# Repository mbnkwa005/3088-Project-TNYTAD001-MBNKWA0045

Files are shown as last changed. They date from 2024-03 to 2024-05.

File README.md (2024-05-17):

# EEE3088F Micro-Mouse Project

### Authors
- Tadiwa Tanyanyiwa
- Kwanele Mabanga

Welcome to the GitHub repository for our project!, which includes two key submodules: the Power submodule and the Sensing submodule.
This repository serves as a central hub for managing and sharing all the relevant files, including datasheets, schematics, and code associated with each submodule.

## Submodules

### Power Submodule
The Power submodule is responsible for supplying the necessary electrical power to all components of the project. 
It ensures that all components are properly powered under different operational conditions.

### Sensing Submodule
The Sensing submodule deals with acquiring data from the physical environment through sensors.

## Repository Contents

- **Datasheets** - Contains all the technical datasheets for components used in both submodules. This includes information on specifications, usage, and limitations of components such as sensors and power management chips.

- **Schematics/Documentation** - Provides detailed pdf schematics for the design and layout of the electrical circuits used in the project. This includes diagrams for both the Power and Sensing submodules as well as the BOM files for each submodule

- **KiCad** - This folder contains all the KiCad Gerber files and KiCad schematics for each subsection.
- **Software** - This folder contains the code used to test the functionalty of the sensing subsystem.
  
### What Hardware you will need
- An STM32L476 Microcontroller
- STM Discovry Board with a STM32F051 Microcontroller (For Testing)
- A micro USB cable to flash code into the STM32FO microcontroller.

### What Software you will need
- STM32CubeIDE 1.13.1 (or newer version) or VSCode with STM32 Extension
- KiCAD 7.0 (or newer version)

## Additional Resources

For more information on specific components or for help with the setup and operation of the submodules, please refer to the datasheets and schematics found in their respective directories within this repository.

## Acknowledgments
Thank you to the UCT Electrical Engineering Department for allowing us to do this cool project!

## Contact

For further inquiries or issues, please contact Tadiwa (tnytad001@myuct.ac.za) and Kwanele (mbnkwa005@myuct.ac.za).

Thank you for visiting our project repository!

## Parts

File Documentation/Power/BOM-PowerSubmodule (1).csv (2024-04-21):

Comment | Designator | Footprint | LCSC
1k | R1,R2,R3,R4 | R_0402_1005Metric | C11702
0.01uF | C3 | C_0402_1005Metric | C15195
0.1uF | C1 | C_0402_1005Metric | C1525
10uF | C2,C5 | C_0603_1608Metric | C19702
LED | D1 | LED_0603_1608Metric | C2286
LED | D2 | LED_0805_2012Metric | C2297
10k | R5 | R_0402_1005Metric | C25744
DRV8833PWP | U2 | HTSSOP-16-1EP_4.4x5mm_P0.65mm_EP3.4x5mm_Mask2.46x2.31mm_ThermalVias | C50506
TP4056 | U1 | SOP127P600X175-9N | C725790
2.2uF | C4 | C_0402_1005Metric

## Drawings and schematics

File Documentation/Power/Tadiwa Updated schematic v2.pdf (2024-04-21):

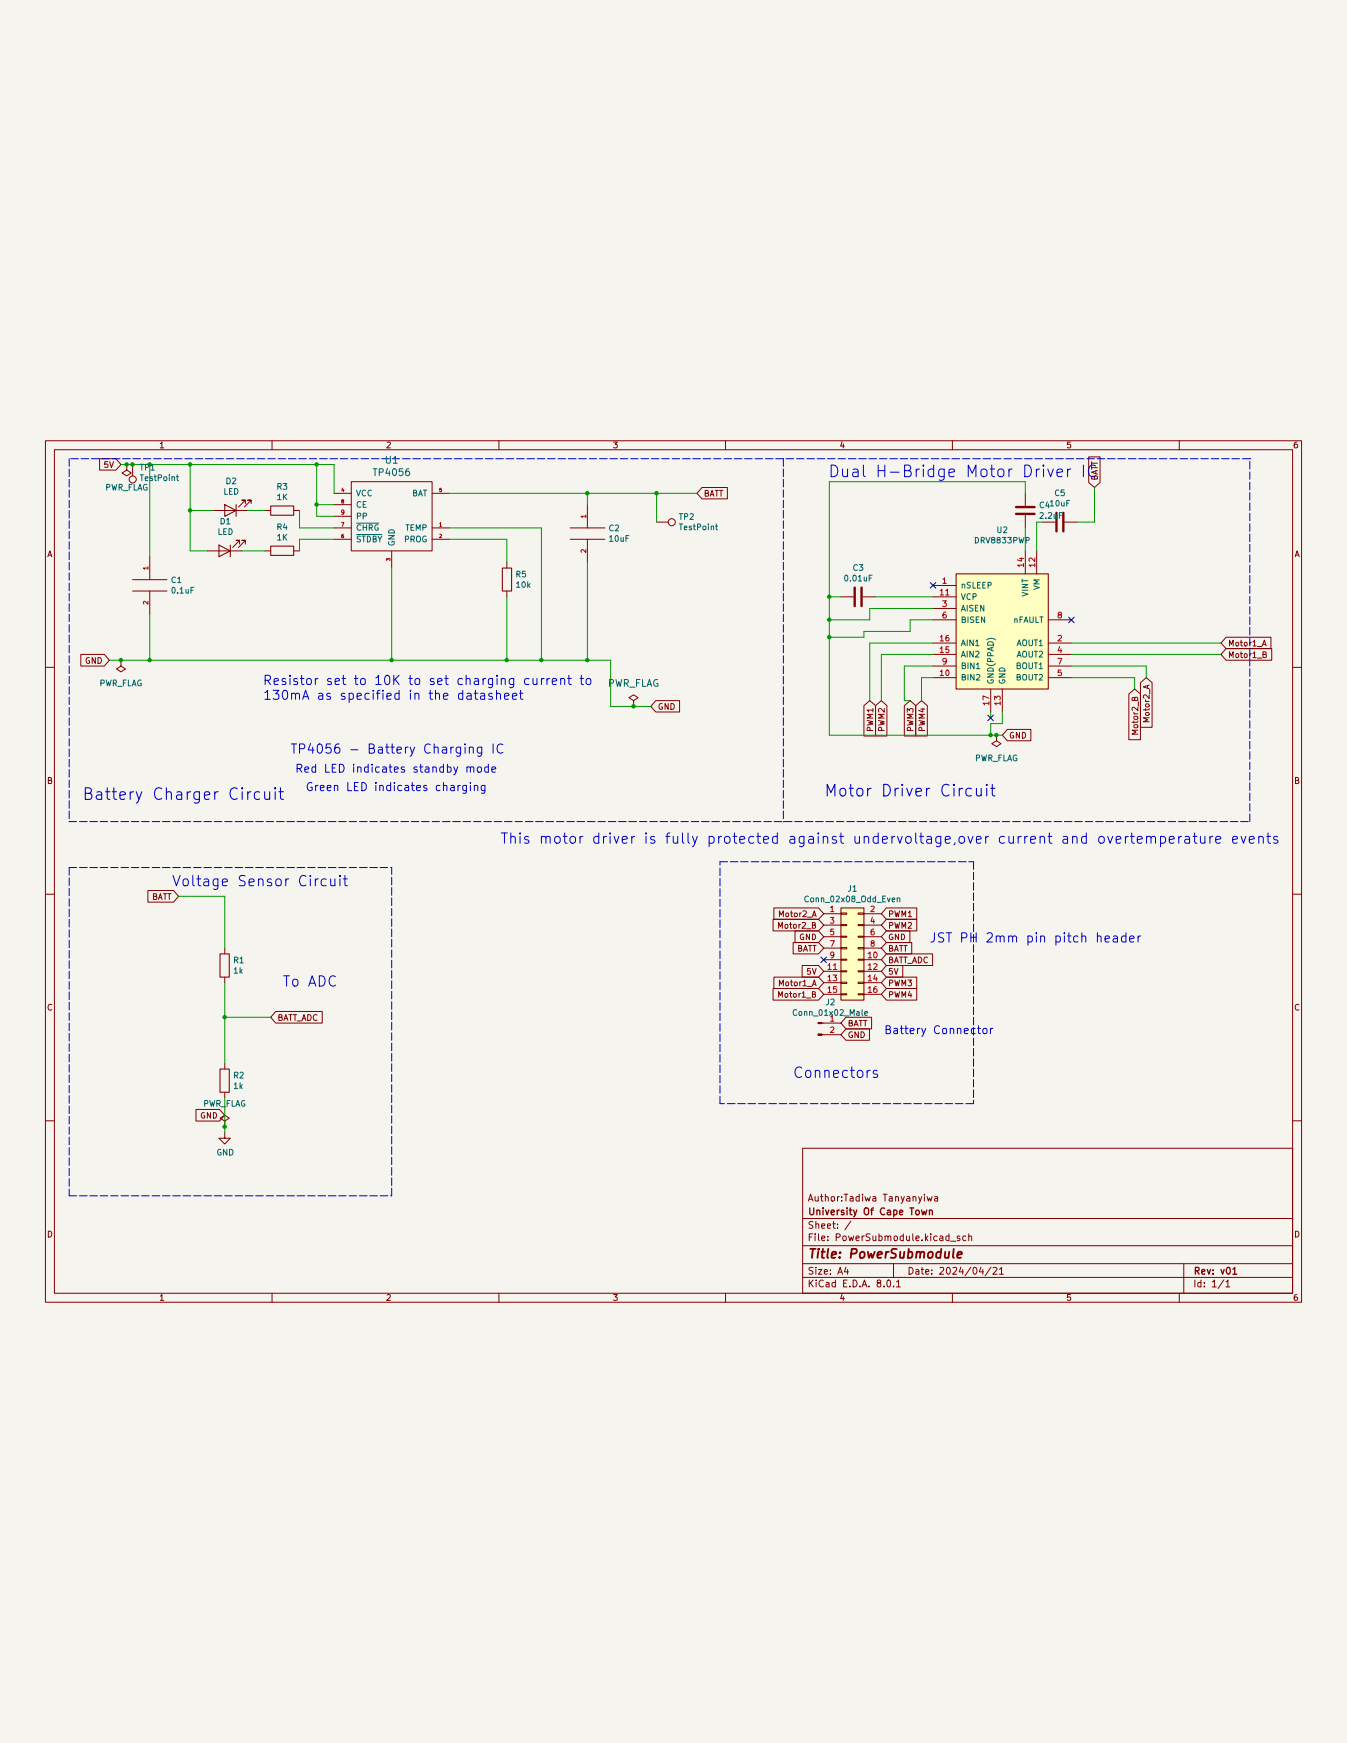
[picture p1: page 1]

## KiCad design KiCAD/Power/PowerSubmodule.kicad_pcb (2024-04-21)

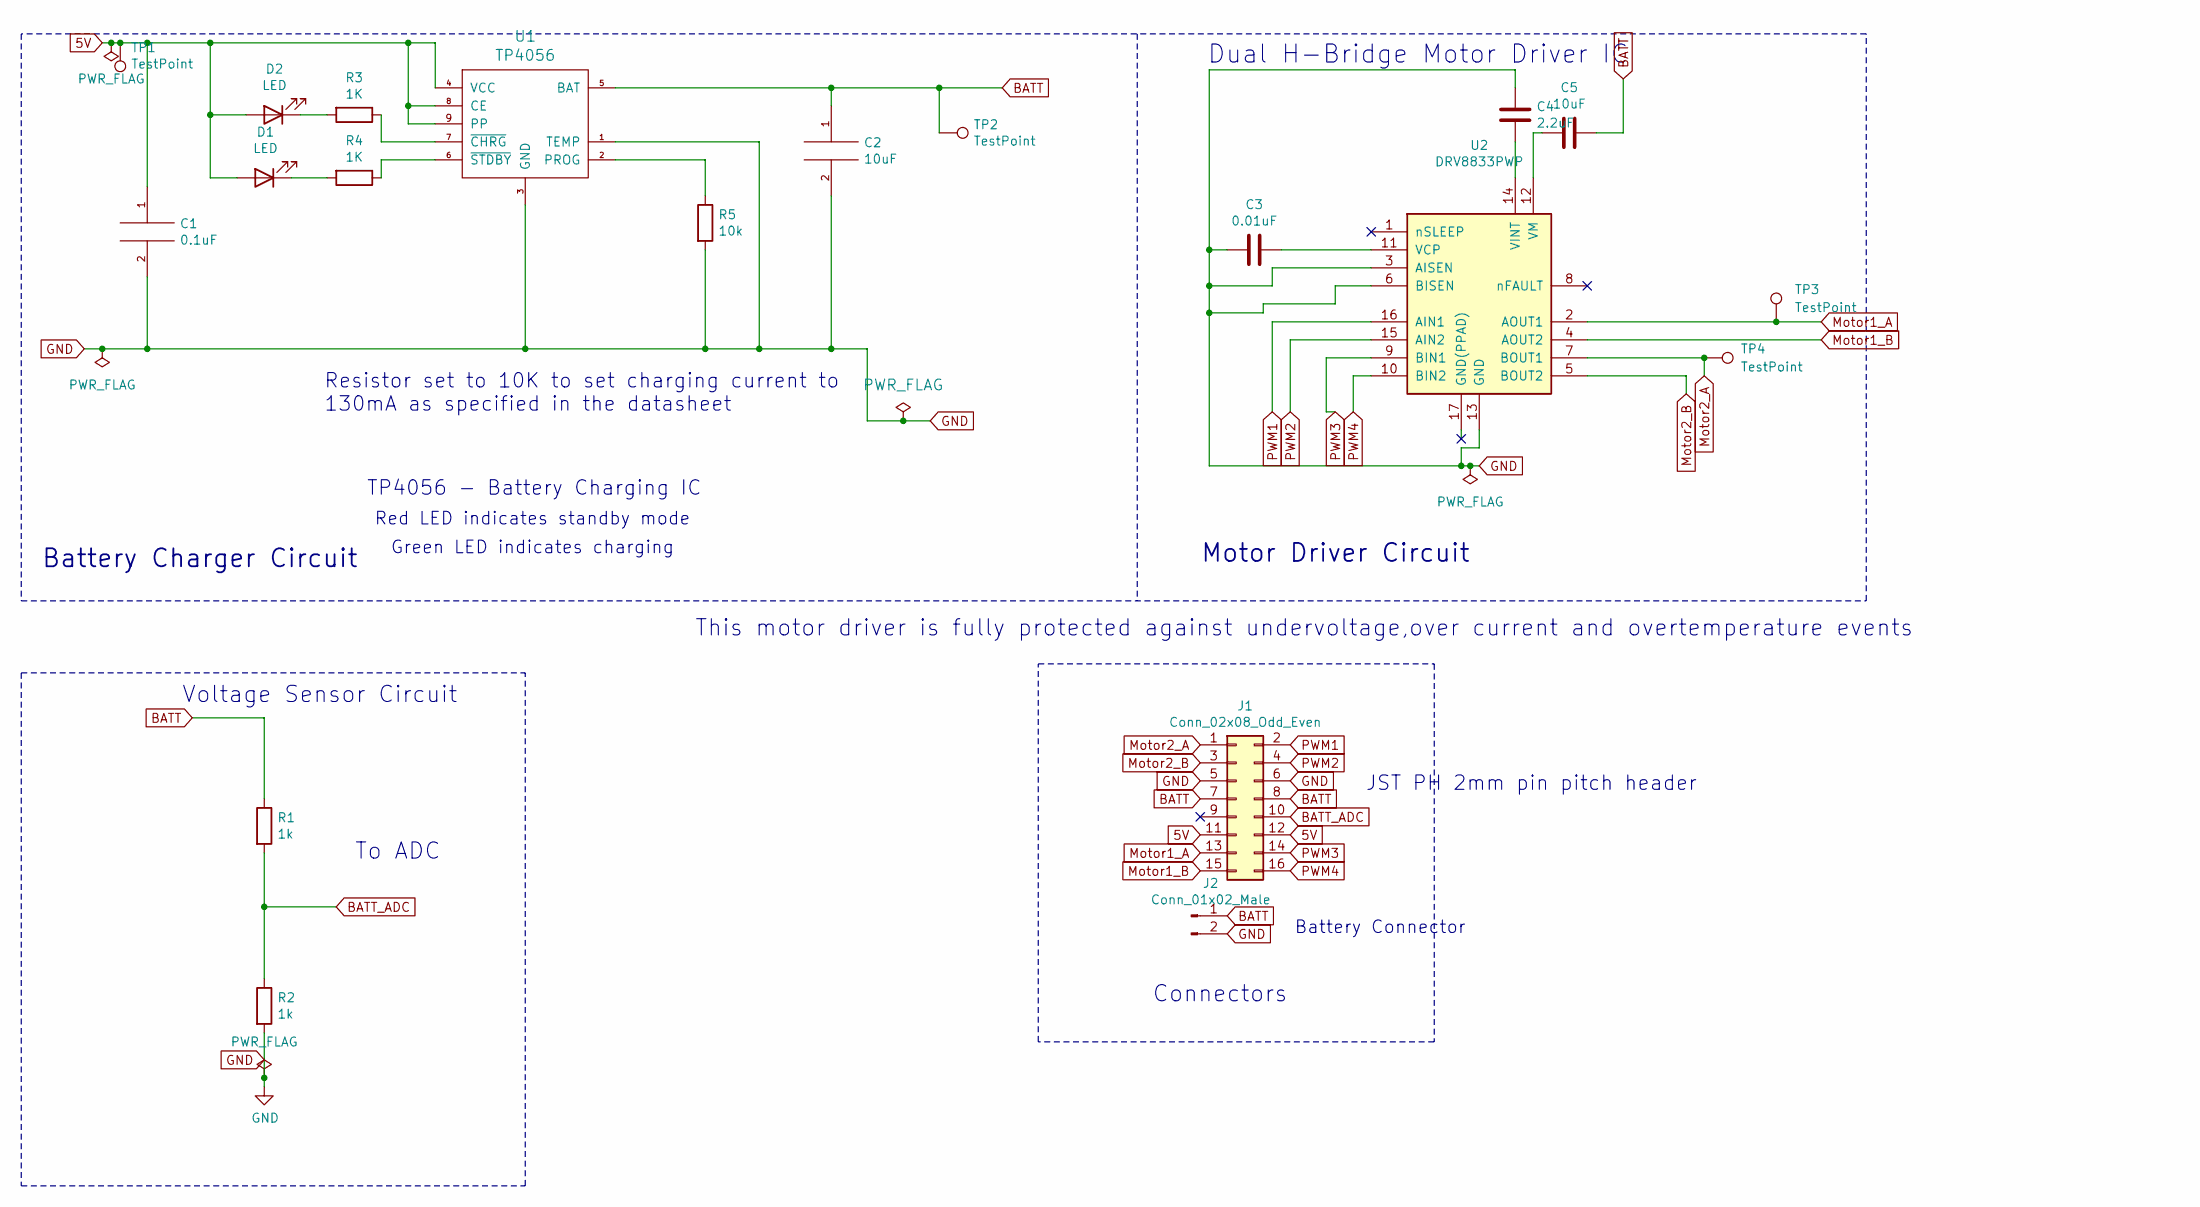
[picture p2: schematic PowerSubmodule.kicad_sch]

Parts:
C1: 0.1uF; C_0402_1005Metric
C2, C5: 10uF; C_0603_1608Metric
C3: 0.01uF; C_0402_1005Metric
C4: 2.2uF; C_0402_1005Metric
D1: LED; LED_0603_1608Metric
D2: LED; LED_0805_2012Metric
J1: Conn_02x08_Odd_Even; PinHeader_2x08_P2.54mm_Vertical
J2: Conn_01x02_Male; JST_JWPF_B02B-JWPF-SK-R_1x02_P2.00mm_Vertical
R1, R2: 1k; R_0402_1005Metric
R3, R4: 1K; R_0402_1005Metric
R5: 10k; R_0402_1005Metric
TP1: TestPoint; TestPoint_THTPad_D1.0mm_Drill0.5mm
TP2: TestPoint; TestPoint_THTPad_D1.5mm_Drill0.7mm
TP3, TP4: TestPoint
U1: TP4056; SOP127P600X175-9N
U2: DRV8833PWP; HTSSOP-16-1EP_4.4x5mm_P0.65mm_EP3.4x5mm_Mask2.46x2.31mm_The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

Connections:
5V: C1.1, D1.2 (A), D2.2 (A), J1.11, J1.12, TP1.1, U1.4 (VCC), U1.8 (CE), U1.9 (PP)
BATT: C2.1, C5.1, J1.7, J1.8, J2.1, R1.1, TP2.1, U1.5 (BAT)
BATT_ADC: J1.10, R1.2, R2.1
GND: C1.2, C2.2, C3.1, C4.1, J1.5, J1.6, J2.2, R2.2, R5.2, U1.1 (TEMP), U1.3 (GND), U2.3 (AISEN), U2.6 (BISEN), U2.13 (GND)
Motor1_A: J1.13, TP3.1, U2.2 (AOUT1)
Motor1_B: J1.15, U2.4 (AOUT2)
Motor2_A: J1.1, TP4.1, U2.7 (BOUT1)
Motor2_B: J1.3, U2.5 (BOUT2)
unnamed: D1.1 (K), R4.2
unnamed: D2.1 (K), R3.2
unnamed: R5.1, U1.2 (PROG)
unnamed: R3.1, U1.7 (~CHRG)
unnamed: R4.1, U1.6 (~STDBY)
unnamed: C3.2, U2.11 (VCP)
unnamed: C4.2, U2.14 (VINT)
unnamed: C5.2, U2.12 (VM)
PWM1: J1.2, U2.16 (AIN1)
PWM2: J1.4, U2.15 (AIN2)
PWM3: J1.14, U2.9 (BIN1)
PWM4: J1.16, U2.10 (BIN2)

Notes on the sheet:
TP4056 - Battery Charging IC
Voltage Sensor Circuit
Battery Charger Circuit
This motor driver is fully protected against undervoltage,over current and overtemperature events
Dual H-Bridge Motor Driver IC
Motor Driver Circuit
Resistor set to 10K to set charging current to 130mA as specified in the datasheet
Connectors
Battery Connector
To ADC
Red LED indicates standby mode
Green LED indicates charging
JST PH 2mm pin pitch header

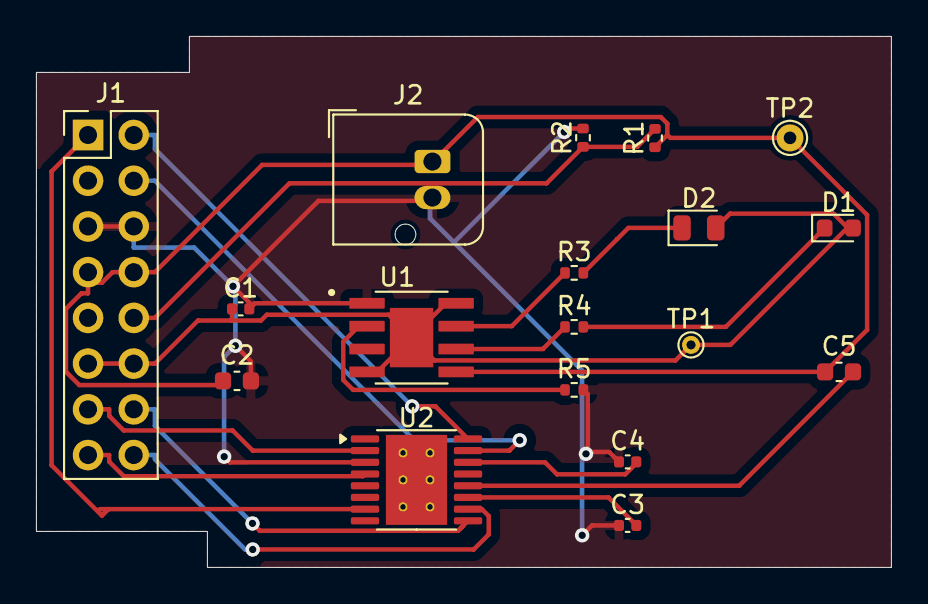
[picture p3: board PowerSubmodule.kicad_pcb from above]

Board: 2 copper layers, 47.5 x 29.5 mm, 18 parts (0 on the bottom side), 20 nets.

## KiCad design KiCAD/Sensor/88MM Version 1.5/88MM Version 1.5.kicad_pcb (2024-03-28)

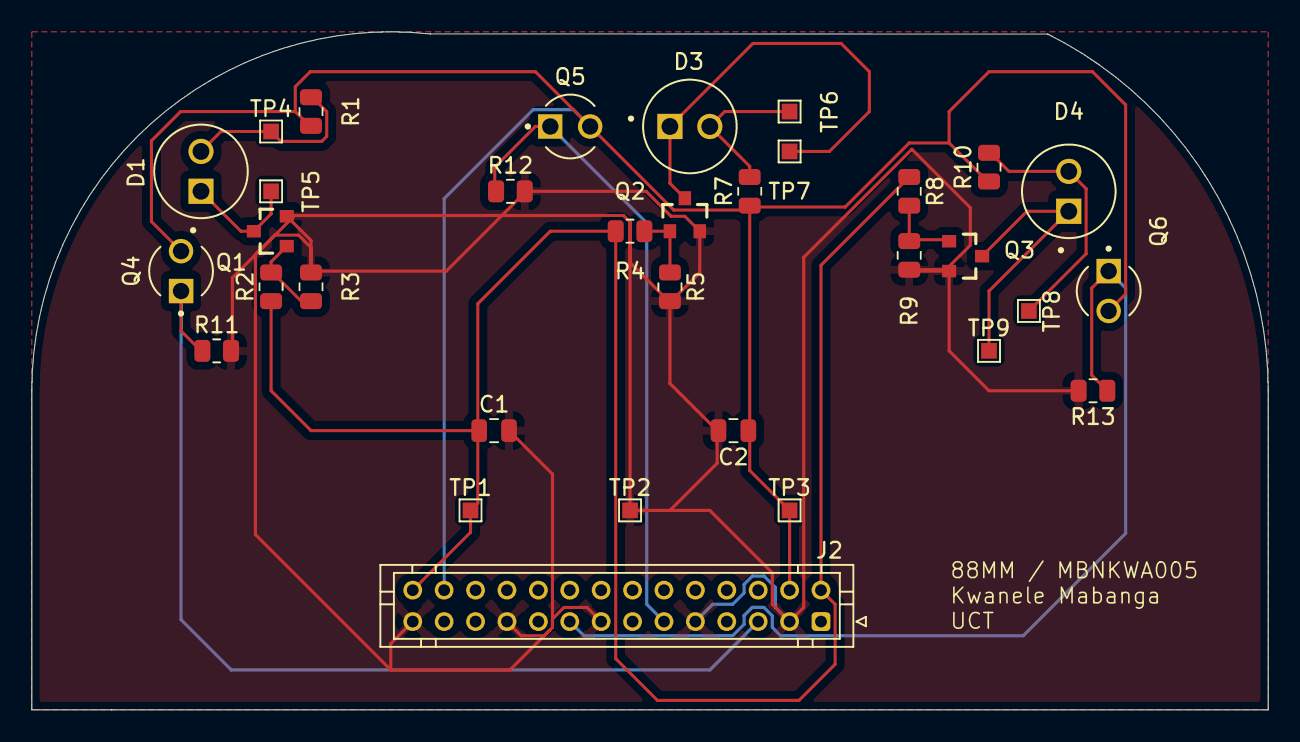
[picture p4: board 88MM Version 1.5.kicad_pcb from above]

Board: 2 copper layers, 78.7 x 43.2 mm, 33 parts (0 on the bottom side), 15 nets.

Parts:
C1, C2: 10nF; C_0805_2012Metric
D1, D3, D4: TSAL6200; LEDRD254W55D595H900
J2: Conn_02x14_Odd_Even; JST_PHD_B28B-PHDSS_2x14_P2.00mm_Vertical
Q1, Q2, Q3: MMBT5551; SOT23-3
Q4, Q5, Q6: TEFT4300; XDCR_TEFT4300
R1, R7, R10: 220; R_0805_2012Metric
R2, R4, R8: 100; R_0805_2012Metric
R3, R5, R9, R11, R12, R13: 10k; R_0805_2012Metric
TP1, TP2, TP3, TP4, TP5, TP6, TP7, TP8, TP9: TestPoint; TestPoint_Pad_1.0x1.0mm

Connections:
+3V3: C1.1, J2.2, J2.28, R2.1, R4.1, R8.1, TP1.1
+BATT: C2.1, J2.4, J2.26, Q4.C, Q5.C, Q6.C, R1.1, R7.1, R10.1, TP3.1
/IR_LED_1A: D1.A, R1.2, TP4.1
/IR_LED_2A: D3.A, R7.2, TP6.1
/IR_LED_2C: D3.C, Q2.3, TP7.1
/IR_LED_3A: D4.A, R10.2, TP8.1
/IR_LED_3C: D4.C, Q3.3, TP9.1
/IR_LED_C: D1.C, Q1.3, TP5.1
/PA3: J2.5, Q4.E, R11.1
/PA5: J2.11, Q5.E, R12.1
/PA7: J2.17, Q6.E, R13.1
GND: C1.2, C2.2, J2.3, J2.9, J2.15, J2.21, J2.27, Q1.2, Q2.2, Q3.2, R3.2, R5.2, R9.2, R11.2, R12.2, R13.2, TP2.1
unnamed: Q1.1, R2.2, R3.1
unnamed: Q2.1, R4.2, R5.1
unnamed: Q3.1, R8.2, R9.1

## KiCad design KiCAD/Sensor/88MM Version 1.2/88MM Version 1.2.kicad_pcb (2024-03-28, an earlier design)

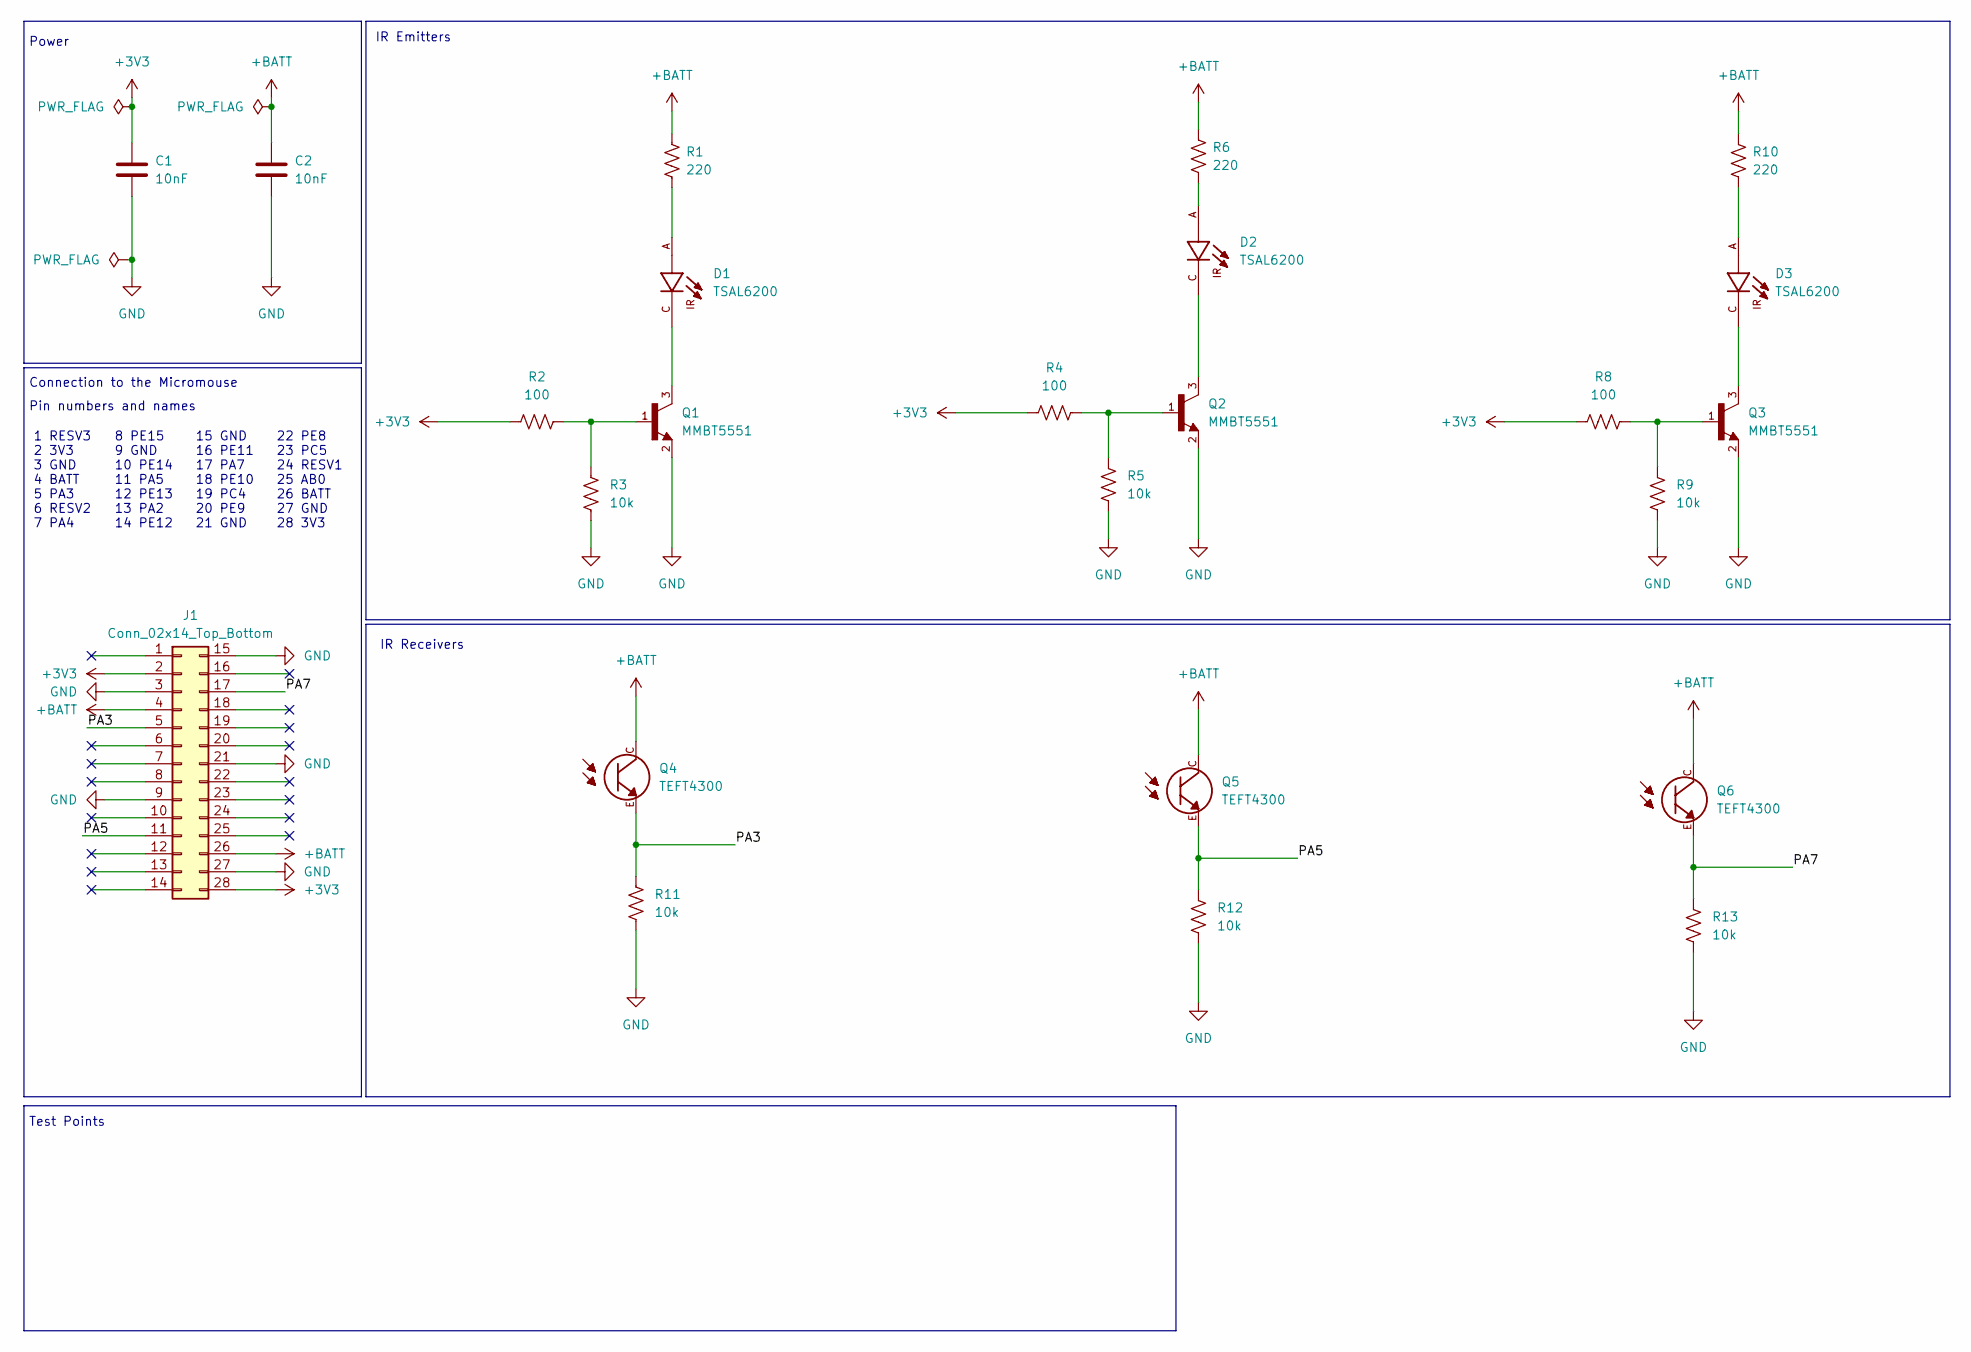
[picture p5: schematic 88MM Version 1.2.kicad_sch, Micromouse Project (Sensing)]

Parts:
C1, C2: 10nF; C_0805_2012Metric_Pad1.18x1.45mm_HandSolder
D1, D2, D3: TSAL6200; LEDRD254W55D595H900; PARTREV 2.4
J1: Conn_02x14_Top_Bottom; JST_PHD_B28B-PHDSS_2x14_P2.00mm_Vertical
Q1, Q2, Q3: MMBT5551; SOT23-3
Q4, Q5, Q6: TEFT4300; XDCR_TEFT4300; DigiKey_Part_Number 751-1041-ND
R1, R6, R10: 220; R_Axial_DIN0207_L6.3mm_D2.5mm_P2.54mm_Vertical
R2, R4, R8: 100; R_Axial_DIN0207_L6.3mm_D2.5mm_P2.54mm_Vertical
R3, R5, R9, R11, R12, R13: 10k; R_Axial_DIN0207_L6.3mm_D2.5mm_P2.54mm_Vertical

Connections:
+3V3: C1.1, J1.2, J1.28, R2.1, R4.1, R8.1
+BATT: C2.1, J1.4, J1.26, Q4.C, Q5.C, Q6.C, R1.1, R6.1, R10.1
/PA3: J1.5, Q4.E, R11.1
/PA5: J1.11, Q5.E, R12.1
/PA7: J1.17, Q6.E, R13.1
GND: C1.2, C2.2, J1.3, J1.9, J1.15, J1.21, J1.27, Q1.2, Q2.2, Q3.2, R3.2, R5.2, R9.2, R11.2, R12.2, R13.2
unnamed: D1.A, R1.2
unnamed: D1.C, Q1.3
unnamed: D2.A, R6.2
unnamed: D2.C, Q2.3
unnamed: D3.A, R10.2
unnamed: D3.C, Q3.3
unnamed: Q1.1, R2.2, R3.1
unnamed: Q2.1, R4.2, R5.1
unnamed: Q3.1, R8.2, R9.1

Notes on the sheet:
Connection to the Micromouse
Test Points
IR Receivers
Pin numbers and names
IR Emitters
22 PE8 23 PC5 24 RESV1 25 AB0 26 BATT 27 GND 28 3V3
1 RESV3 2 3V3 3 GND 4 BATT 5 PA3 6 RESV2 7 PA4
Power
15 GND 16 PE11 17 PA7 18 PE10 19 PC4 20 PE9 21 GND
8 PE15 9 GND 10 PE14 11 PA5 12 PE13 13 PA2 14 PE12

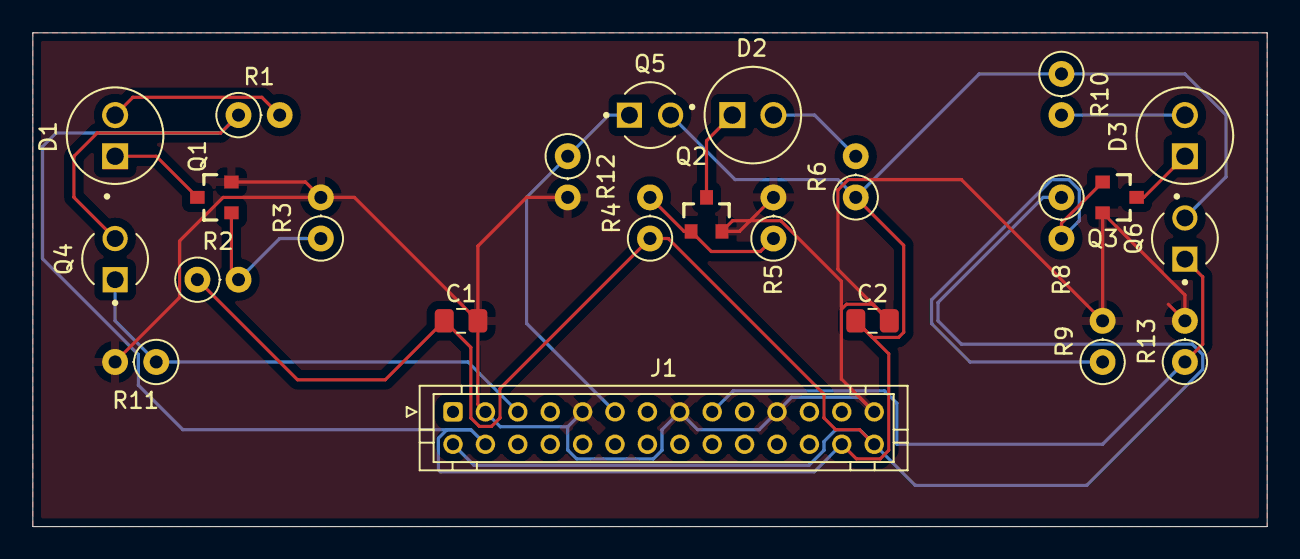
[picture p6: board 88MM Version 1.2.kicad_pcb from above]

Board: 2 copper layers, 76.2 x 30.5 mm, 24 parts (0 on the bottom side), 15 nets.

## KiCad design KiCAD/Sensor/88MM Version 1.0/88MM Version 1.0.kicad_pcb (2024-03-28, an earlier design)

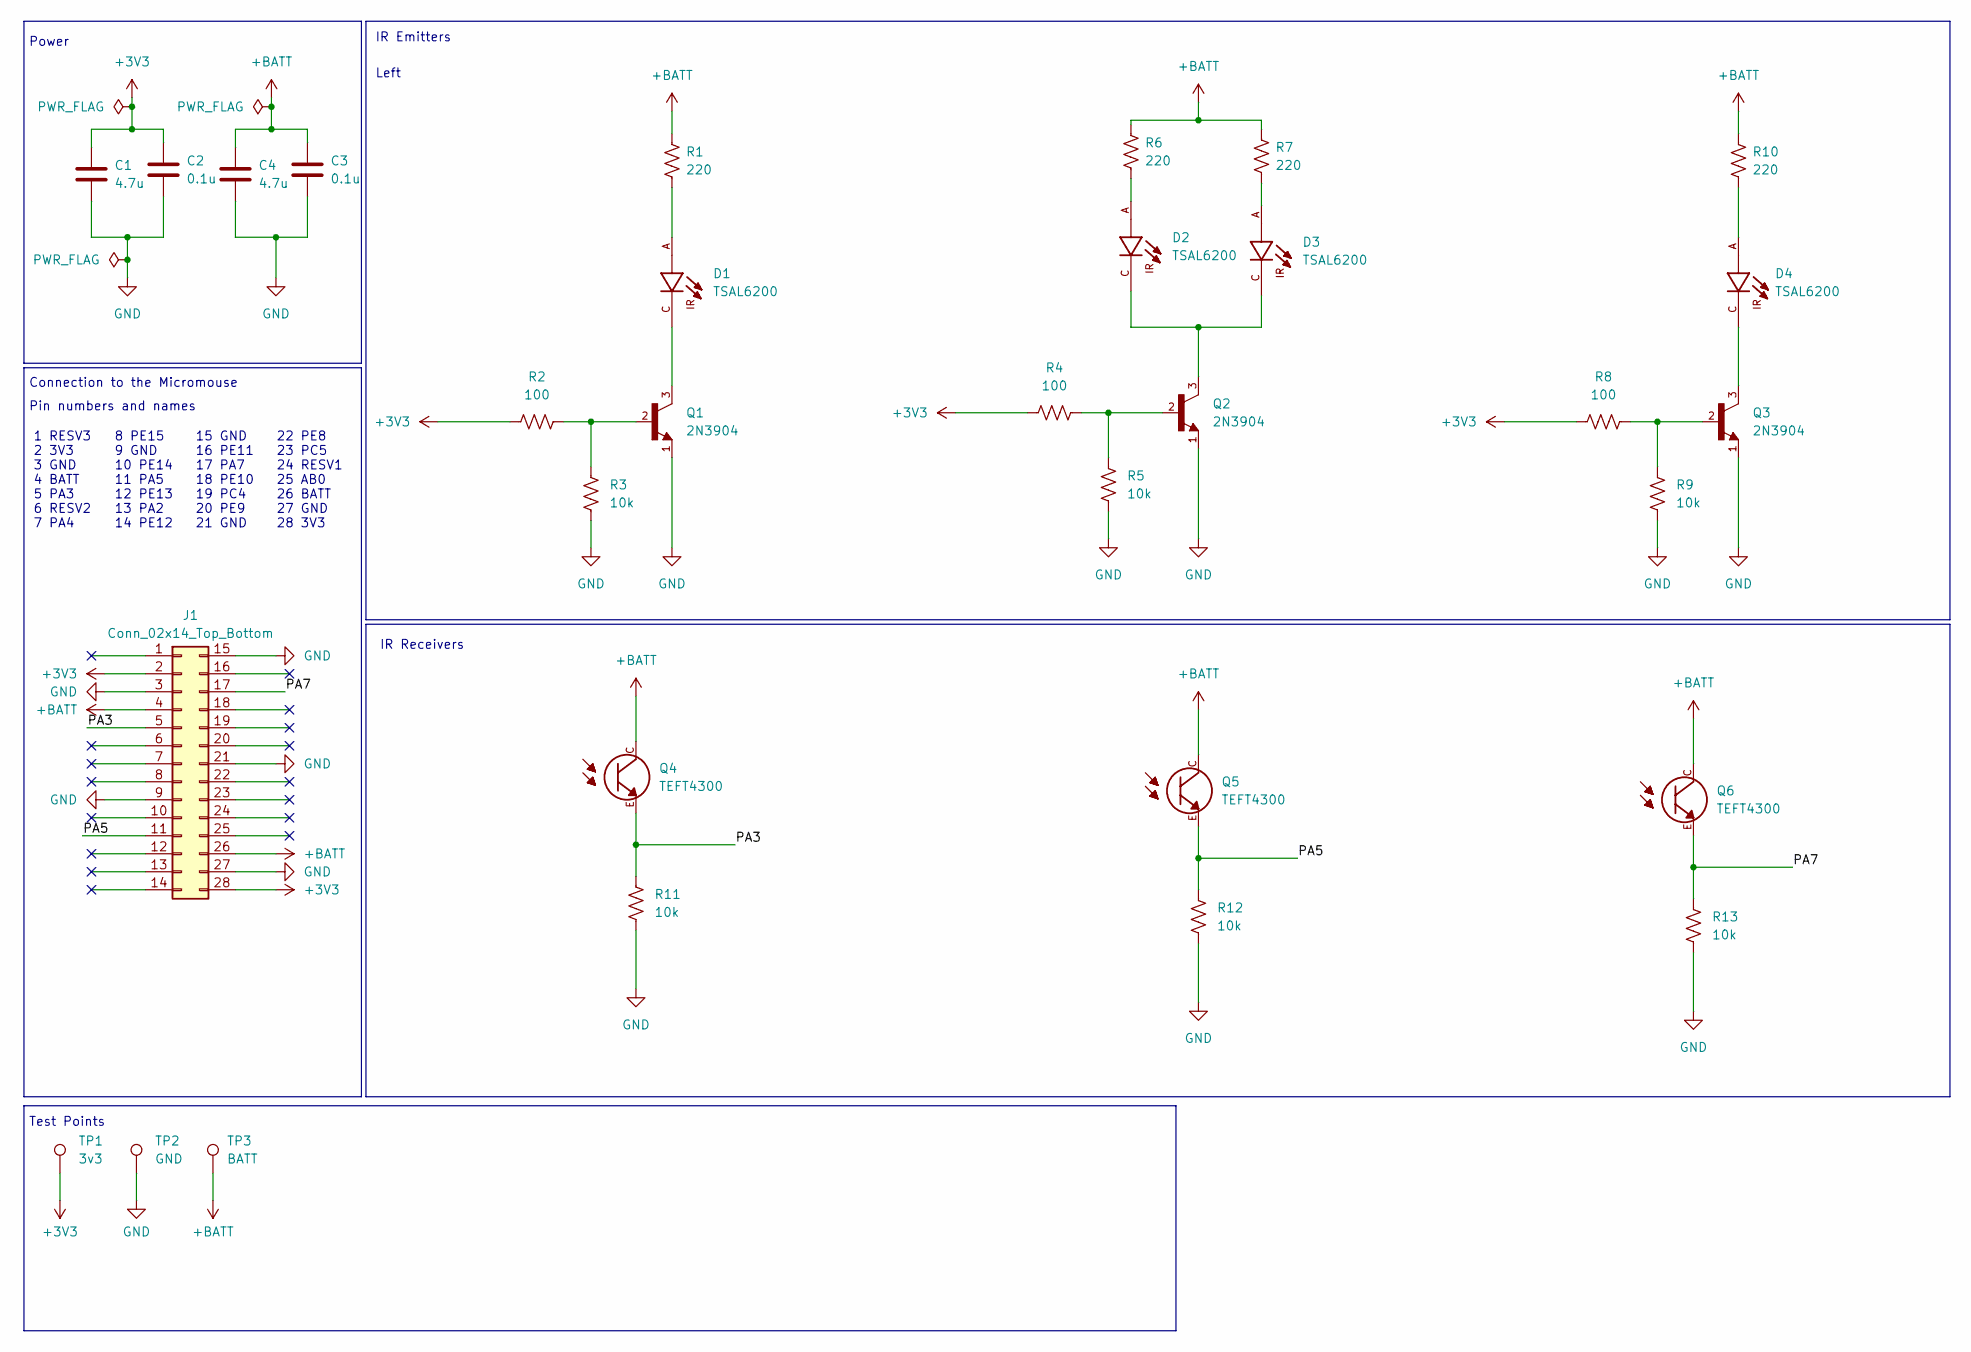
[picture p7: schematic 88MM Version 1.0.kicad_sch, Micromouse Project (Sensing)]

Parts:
C1, C4: 4.7u; CP_Radial_D5.0mm_P2.00mm
C2, C3: 0.1u; CP_Radial_D5.0mm_P2.00mm
D1, D2, D3, D4: TSAL6200; LEDRD254W55D595H900; PARTREV 2.4
J1: Conn_02x14_Top_Bottom; JST_PHD_B28B-PHDSS_2x14_P2.00mm_Vertical
Q1, Q2, Q3: 2N3904; TO92127P495H495-3; PARTREV February 2003
Q4, Q5, Q6: TEFT4300; XDCR_TEFT4300; DigiKey_Part_Number 751-1041-ND
R1, R6, R7, R10: 220; R_Axial_DIN0207_L6.3mm_D2.5mm_P2.54mm_Vertical
R2, R4, R8: 100; R_Axial_DIN0207_L6.3mm_D2.5mm_P2.54mm_Vertical
R3, R5, R9, R11, R12, R13: 10k; R_Axial_DIN0207_L6.3mm_D2.5mm_P2.54mm_Vertical
TP1: 3v3; TestPoint_Pad_D1.0mm
TP2: GND; TestPoint_Pad_D1.0mm
TP3: BATT; TestPoint_Pad_D1.0mm

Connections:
+3V3: C1.1, C2.1, J1.2, J1.28, R2.1, R4.1, R8.1, TP1.1
+BATT: C3.1, C4.1, J1.4, J1.26, Q4.C, Q5.C, Q6.C, R1.1, R6.1, R7.1, R10.1, TP3.1
/PA3: J1.5, Q4.E, R11.1
/PA5: J1.11, Q5.E, R12.1
/PA7: J1.17, Q6.E, R13.1
GND: C1.2, C2.2, C3.2, C4.2, J1.3, J1.9, J1.15, J1.21, J1.27, Q1.1, Q2.1, Q3.1, R3.2, R5.2, R9.2, R11.2, R12.2, R13.2, TP2.1
unnamed: D1.A, R1.2
unnamed: D1.C, Q1.3
unnamed: D2.A, R6.2
unnamed: D2.C, D3.C, Q2.3
unnamed: D3.A, R7.2
unnamed: D4.A, R10.2
unnamed: D4.C, Q3.3
unnamed: Q1.2, R2.2, R3.1
unnamed: Q2.2, R4.2, R5.1
unnamed: Q3.2, R8.2, R9.1

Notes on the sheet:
Connection to the Micromouse
Test Points
IR Receivers
Left
Pin numbers and names
IR Emitters
22 PE8 23 PC5 24 RESV1 25 AB0 26 BATT 27 GND 28 3V3
1 RESV3 2 3V3 3 GND 4 BATT 5 PA3 6 RESV2 7 PA4
Power
15 GND 16 PE11 17 PA7 18 PE10 19 PC4 20 PE9 21 GND
8 PE15 9 GND 10 PE14 11 PA5 12 PE13 13 PA2 14 PE12

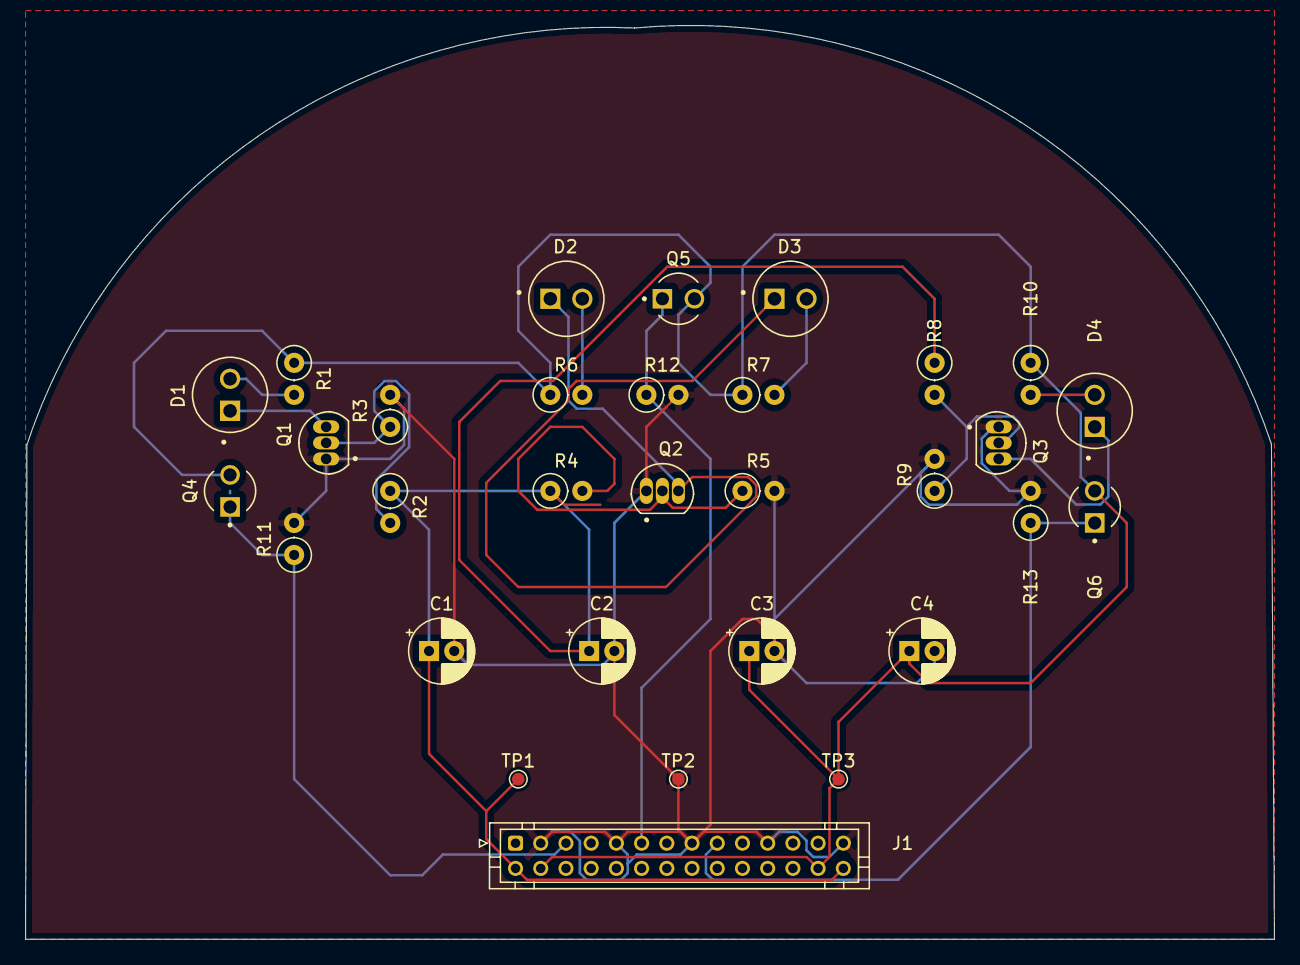
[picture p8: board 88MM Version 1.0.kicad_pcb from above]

Board: 2 copper layers, 99.1 x 72.5 mm, 31 parts (0 on the bottom side), 16 nets.
